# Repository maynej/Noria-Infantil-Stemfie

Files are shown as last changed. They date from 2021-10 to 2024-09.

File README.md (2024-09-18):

# Nòria Infantil Stemfie  

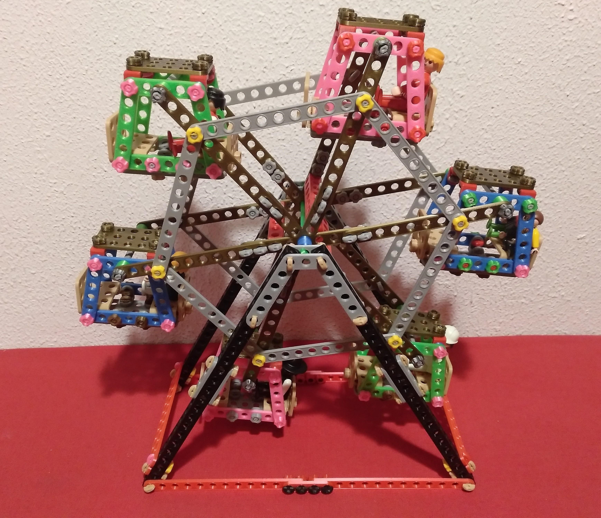
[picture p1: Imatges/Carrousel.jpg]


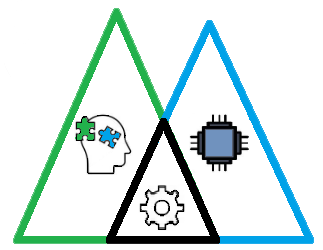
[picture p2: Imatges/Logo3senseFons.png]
Realitzada per [Jordi Mayné](https://github.com/maynej) des de Mechatronic Study 

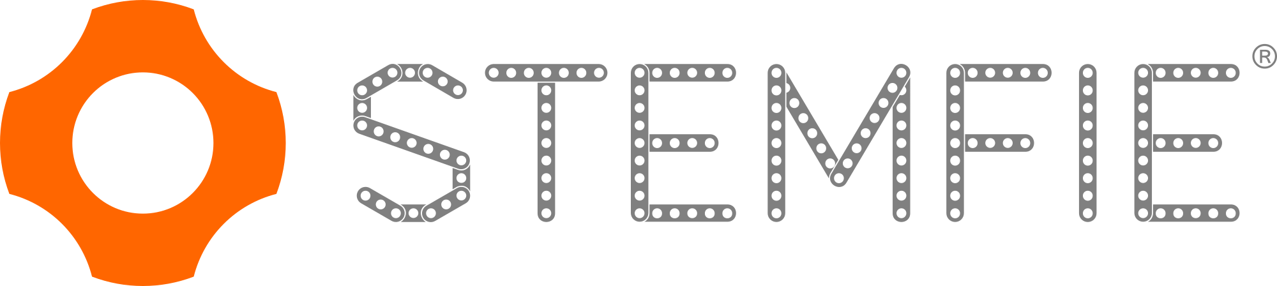
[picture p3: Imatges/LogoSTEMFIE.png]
STEMFIE es un projecte de construcció lliure, que s'imprimeix en 3D (http://stemfie.org) 

Electronics Stemfie es una llibreria STL de suports per tarjes de control, sensors i actuadors amb compatibilitat Stemfie.

[Electronics Suports amb compatibilitat Stemfie](https://github.com/maynej/Electronics-Stemfie), pretén facilitar l'automatització de les construccions amb targes Arduino, Microbit, ESP... 

La documentació està disponible també en castellà i anglés [en PDF](https://github.com/maynej/Carrousel-Stemfie/tree/main/Doc) i un video del muntatge.

STL per imprimir la Cabina [aquí](https://github.com/maynej/Carrousel-Stemfie/tree/main/STL/Cabin)

STL per imprimir la Roda [aquí](https://github.com/maynej/Carrousel-Stemfie/tree/main/STL/Wheel)

STL per imprimir la Base [aquí](https://github.com/maynej/Carrousel-Stemfie/tree/main/STL/Base)

## Cabina 

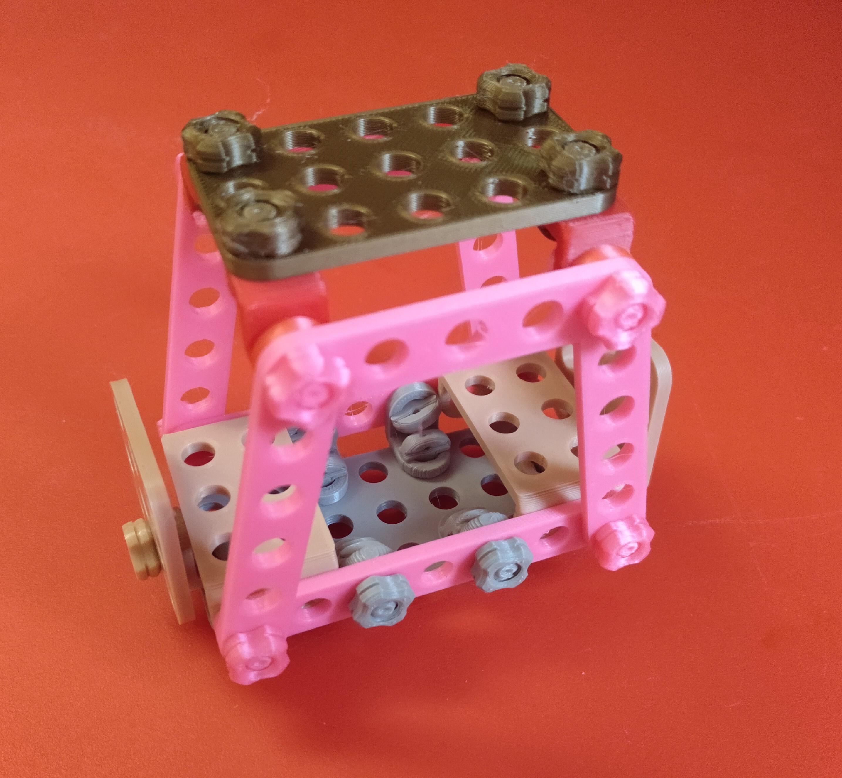
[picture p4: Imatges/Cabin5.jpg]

  
Descripció    | Quantitat     | Imatge          | Arxiu         
------------- | ------------- | --------------- | -----
Tensor 7 | 12  | | [Tensor 7](STL/Cabin/Brace_7-SPN-BRC-0006_x12.stl)
Marc Cabina | 12 | | [Marc Cabina](STL/Cabin/STR_STD_BRT_AZ_5x5x5_x12.stl)
Femella | 144 | | [Femella](STL/Cabin/NutRH-BU01.00x5mm_x144.stl)
Cargol BU00.50 | 96 | | [Cargol BU00.50](STL/Cabin/ScrewRHD-RH-BU00.50_x96.stl)
Cargol BU00.75 | 48 | | [Cargol BU00.75](STL/Cabin/Screw-RHD-RH-BU00.75_x32.stl)
Escaire | 60 | | [Escaire](STL/Cabin/STR_STD_BRD_AY-1x1_90_x60.stl)
Seient | 12 | | [Seient](STL/Cabin/STR_STD_BRT-AYx1x3x1_x12.stl)
Placa 3x3 | 12 | | [Placa 3x3](STL/Cabin/STR_STD_BRM_3x3_x12.stl)
Placa 3x5 | 6 | | [Placa 3x5](STL/Cabin/STR_STD_BRM_5x3_x6.stl)
Placa 3x7 | 6 | | [Placa 3x7](STL/Cabin/STR_STD_BRM_7x3_x6.stl)
Volandera 5mm | 24 | | [Volandera 5mm](STL/Cabin/Washer-FRE-BU01.00x00.25_x24.stl)

## Roda 

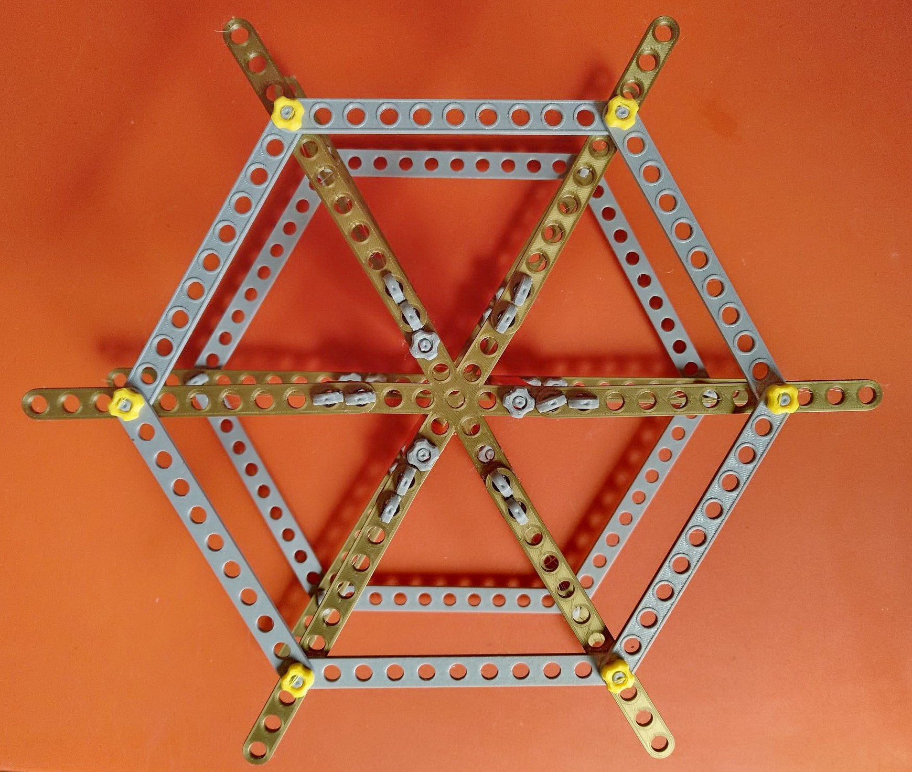
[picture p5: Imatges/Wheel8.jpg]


Descripció    | Quantitat     | Imatge          | Arxiu         
------------- | ------------- | --------------- | ----- 
Tensor 11 | 24  | | [Tensor 11](STL/Wheel/Brace_11_STR_ERR_x24.stl)
Biga 6 | 3 | | [Biga 6](STL/Wheel/beam1x1x6_3.stl)
Creu 9x9x9 | 2  | | [Creu](STL/Wheel/Cross_9x9x9_x2.stl)
Femella | 63 | | [Femella](STL/Wheel/Nut_RH_BU01.00x5mm_x39.stl)
Cargol BU00.50 | 24  | | [Cargol BU00.50](STL/Wheel/Screw_RHD_RH_BU00.50_x24.stl)
Cargol BU00.75 | 12  | | [Cargol BU00.75](STL/Wheel/Screw_RHD_RH_BU00.75_x12.stl)
Cargol BU06.50 | 3   | | [Cargol BU06.50](STL/Wheel/Screw_RHD_RH_BU06.50_x3.stl)
Pin | 6  | | [Pin BU07.00](STL/Wheel/Pin_CL_RHD_BU07.00_x6.stl)
Fixador | 6  | | [Fixador](STL/Wheel/Nut_PH_CL_BU1x5mm.stl)
Volandera 10mm | 12  | | [Volandera 12 mm](STL/Wheel/Washer10mm_12.stl)

## Base 

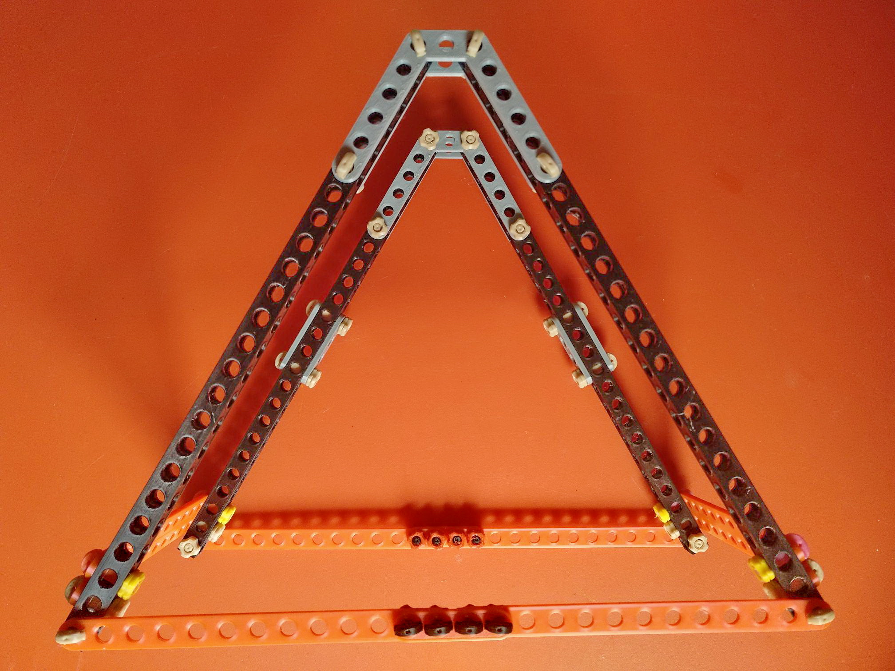
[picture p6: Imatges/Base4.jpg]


Descripció    | Quantitat     | Imatge          | Arxiu         
------------- | ------------- | --------------- | ----- 
Biga 12 | 8 | | [Biga 12](STL/Base/Beam_12_x8.stl)
Tensor 4 | 10  | | [Tensor 4](STL/Base/Brace_4_STR_ERR_BU04x01x00.25_x10.stl)
Tensor 12 | 4  | | [Tensor 12](STL/Base/Brace_12_STR_ERR_BU12x01x00.25x4.stl)
Tensor 13 | 4  | | [Tensor 13](STL/Base/Brace_13_STR_ERR_BU13x01x00.25_x4.stl)
Femella | 44 | | [Femella](STL/Base/Nut_RH_BU01.00x5mm_x44.stl)
Cargol BU00.50 | 8  | | [Cargol BU00.50](STL/Base/Screw_RHD_RH_BU00.50_x8.stl)
Cargol BU01.25 | 12 | | [Cargol BU01.25](STL/Base/Screw_RHD_RH_BU01.25_x12.stl)
Cargol BU01.50 | 16 | | [Cargol BU01.50](STL/Base/Screw_RHD_RH_BU01.50_x16.stl)
Pin | 1  | | [Pin Eix](STL/Base/Pin166.stl)
Fixador | 1  | | [Fixador](STL/Base/Nut_PH_CL_BU1x5mm_x1.stl)
U | 4 | | [U](STL/Base/STR_STD_BRT_AZ_3_5_5_120_x4.stl)
Volandera | 13  | | [Volandera](STL/Base/Washer_FRE_BU01.00x00.25_x13.stl)

## Control 

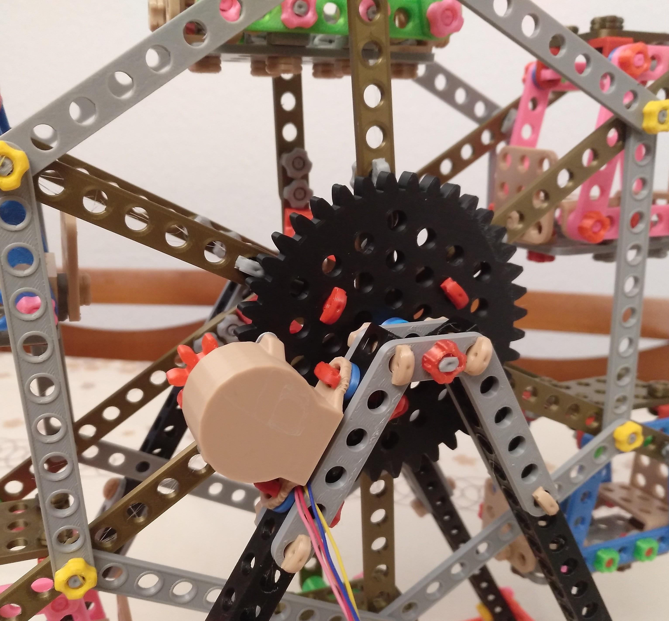
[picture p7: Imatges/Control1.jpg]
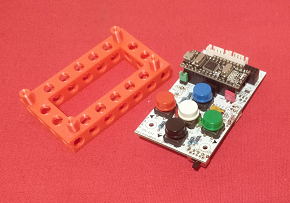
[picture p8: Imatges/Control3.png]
 

Descripció    | Quantitat     | Imatge          | Arxiu         
------------- | ------------- | --------------- | ----- 
Femella | 5 | | [Femella](STL/Control/Nut_RH_BU01.00x5mm_x2.stl)
Cargol BU01.50 | 5 | | [Cargol BU01.50](STL/Control/Screw_RHD_RH_BU01.50_x5.stl)
CPU suport | 1 | | [CPU Suport](STL/Control/CPUEscornaStemfie_x1.stl)
Volandera 2.5mm | 2  | | [Volandera](STL/Control/Washer_FRE_2.5mmx2.stl)
Engranatge motor | 1  | | [Engranatge motor](STL/Control/Gear_28BYJ-48_x1.stl)
Engranatge 40 |  1  | | [Engranatge 40](STL/Control/IGE_0.5_40_M2,5_x1.stl)
Suport motor |  1  | | [Suport motor](STL/Control/28BYJ-48_4H_x1.stl)

## Mesurador Stemfie 

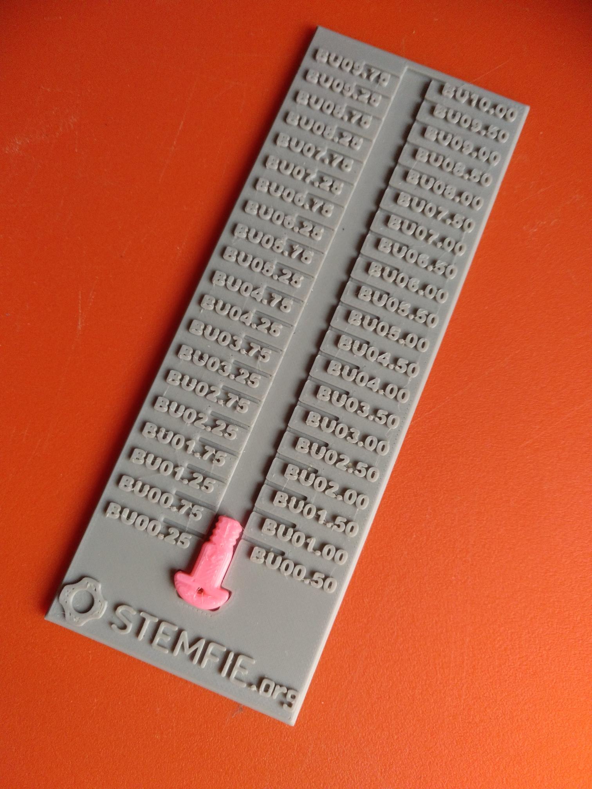
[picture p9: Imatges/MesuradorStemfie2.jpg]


Descripció    | Opcional     | Arxiu         
------------- | ------------ | ----- 
Mesurador Cargols | 1  | [Mesurador](STL/Base/MesuraStemfie2.stl)

## QR


## Llicència

Creative Commons Attribution-NoComercial-ShareAlike 4.0 International (CC BY-NC-SA 4.0)

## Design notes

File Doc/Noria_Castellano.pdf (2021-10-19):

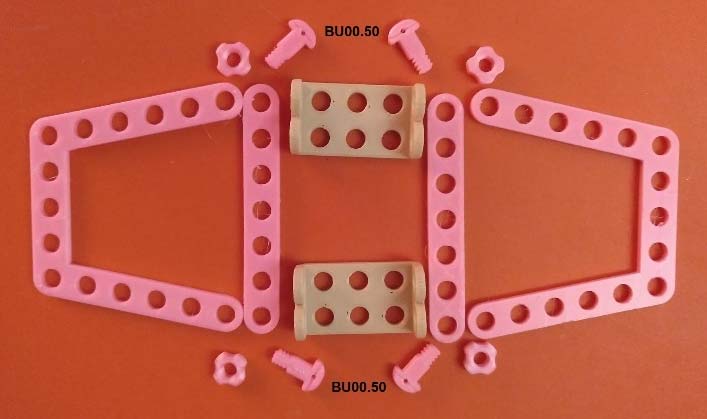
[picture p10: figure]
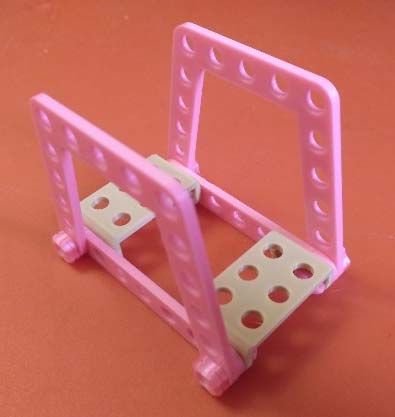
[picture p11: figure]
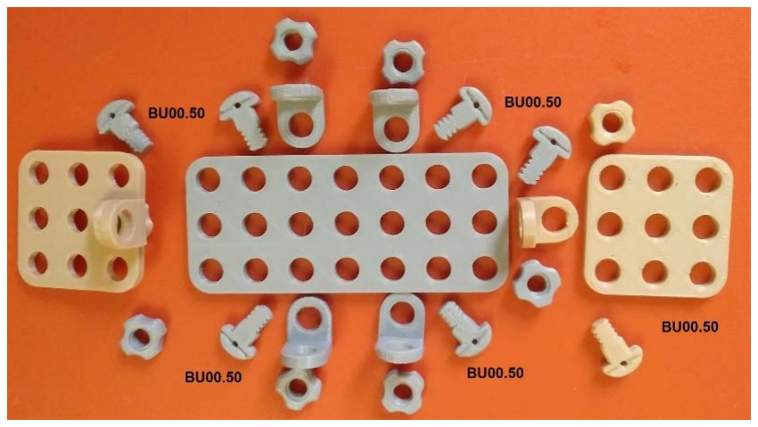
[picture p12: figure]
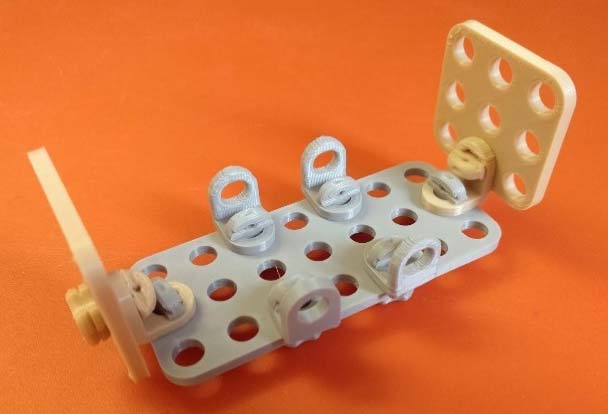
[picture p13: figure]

NORIA INFANTIL V1 – 2021 | 1 | JORDI MAYNE

## Noria Infantil

Esta Noria es una reproducción de la típica atracción infantil hecha con estructura Stemfie.

Permite ser una herramienta de habilidad de montaje para grupos, la conforman 6 cabinas idénticas, las 2 ruedas de soporte de las cabinas y la estructura de la base, es decir que pueden participar hasta 9 jóvenes o adolescentes.

Los tornillos son piezas que actualmente no se usan en los montajes actuales, se unen las piezas a base de ensamblajes fáciles, pero a la vez pierden la oportunidad de coger una habilidad manual y destreza para colocar los mismos y girar la tuercas.

### Montaje

Cabina

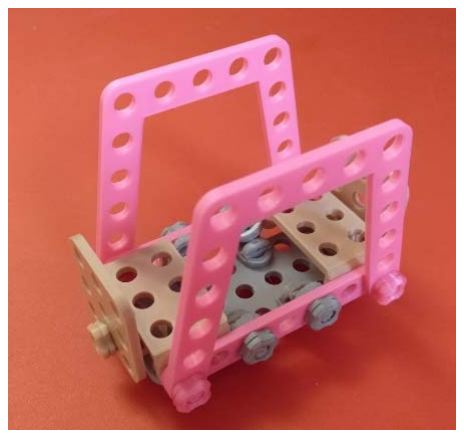
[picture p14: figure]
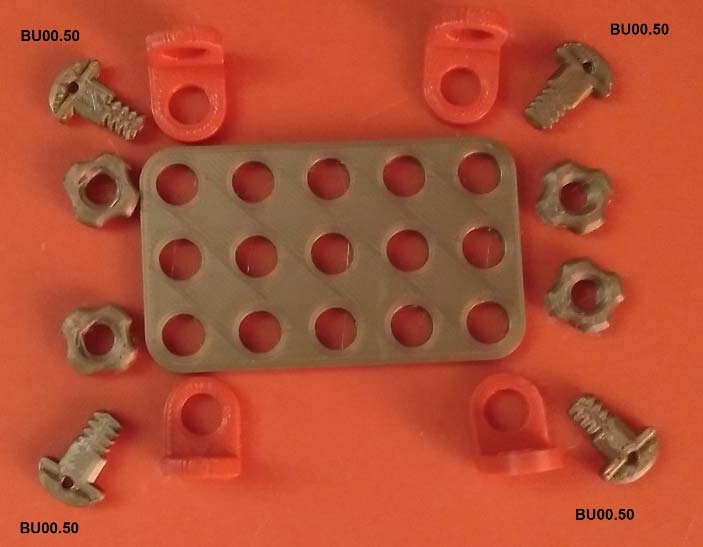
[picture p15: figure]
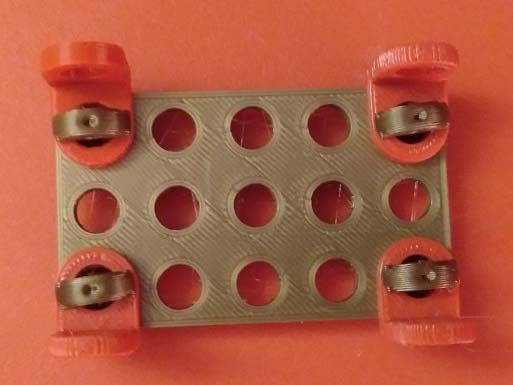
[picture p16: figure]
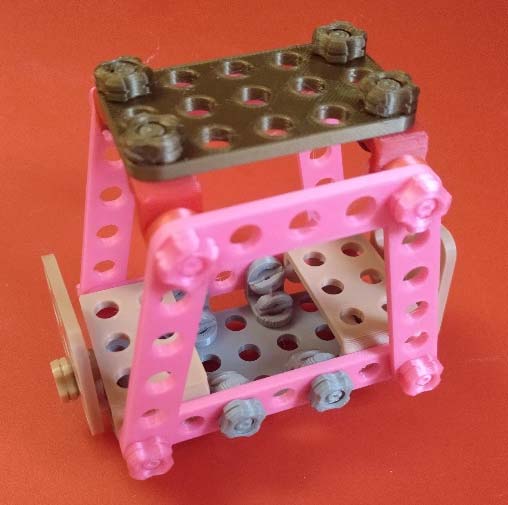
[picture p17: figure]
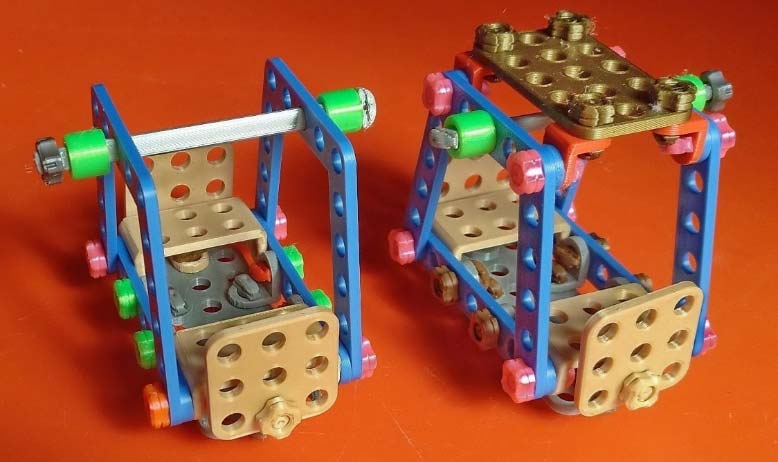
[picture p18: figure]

NORIA INFANTIL V1 – 2021 | 2 | JORDI MAYNE

Si se quiere la versión con techo, para el invierno hace falta añadir este montaje. Los tornillos son del tipo BU00.50

Todos los tormillos son del tipo BU00.50

La cabina puede quedar en este punto, versión sin techo, para el verano.

Para fijar el techo a la cabina hace falta añadir 4 tornillos BU00.75, 4 arabdelas y 4 tuercas.

Se montan 6 cabinas y para fijarlas a la rueda se usa PIN07.00, fijador, y arandelas de 10mm, se verá más adelante este montaje.

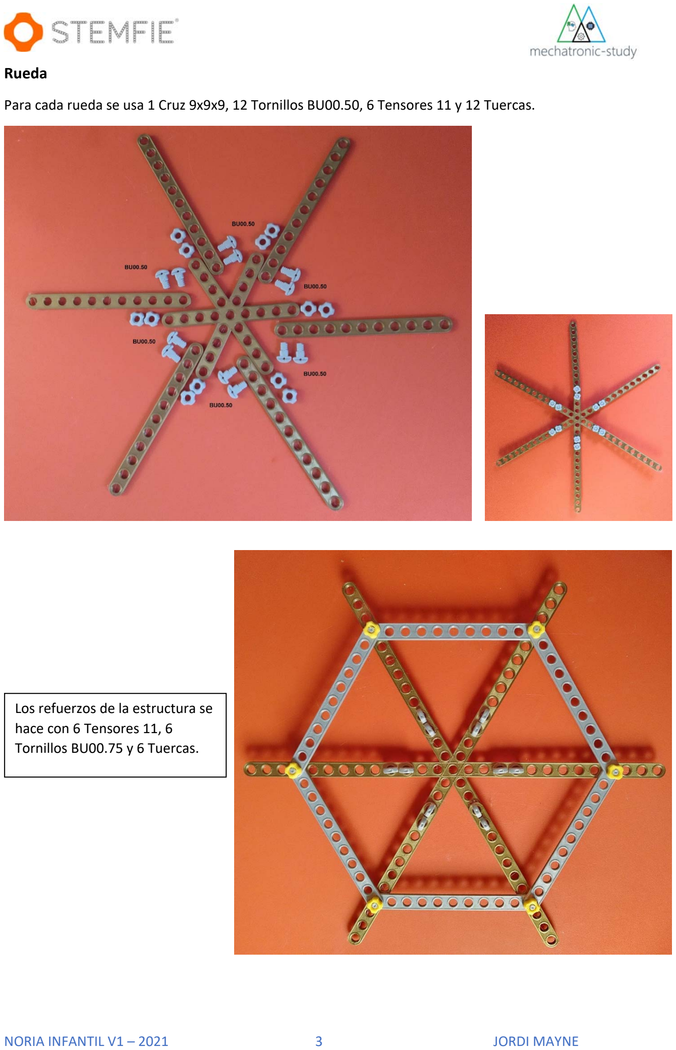
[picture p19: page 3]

NORIA INFANTIL V1 – 2021 | 3 | JORDI MAYNE

Rueda

Para cada rueda se usa 1 Cruz 9x9x9, 12 Tornillos BU00.50, 6 Tensores 11 y 12 Tuercas.

Los refuerzos de la estructura se hace con 6 Tensores 11, 6
Tornillos BU00.75 y 6 Tuercas.

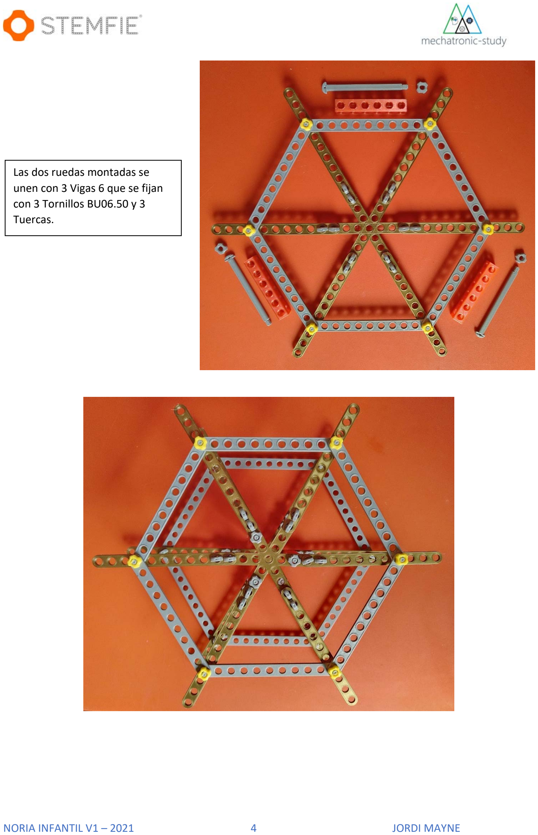
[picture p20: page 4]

NORIA INFANTIL V1 – 2021 | 4 | JORDI MAYNE

Las dos ruedas montadas se unen con 3 Vigas 6 que se fijan con 3 Tornillos BU06.50 y 3 Tuercas.

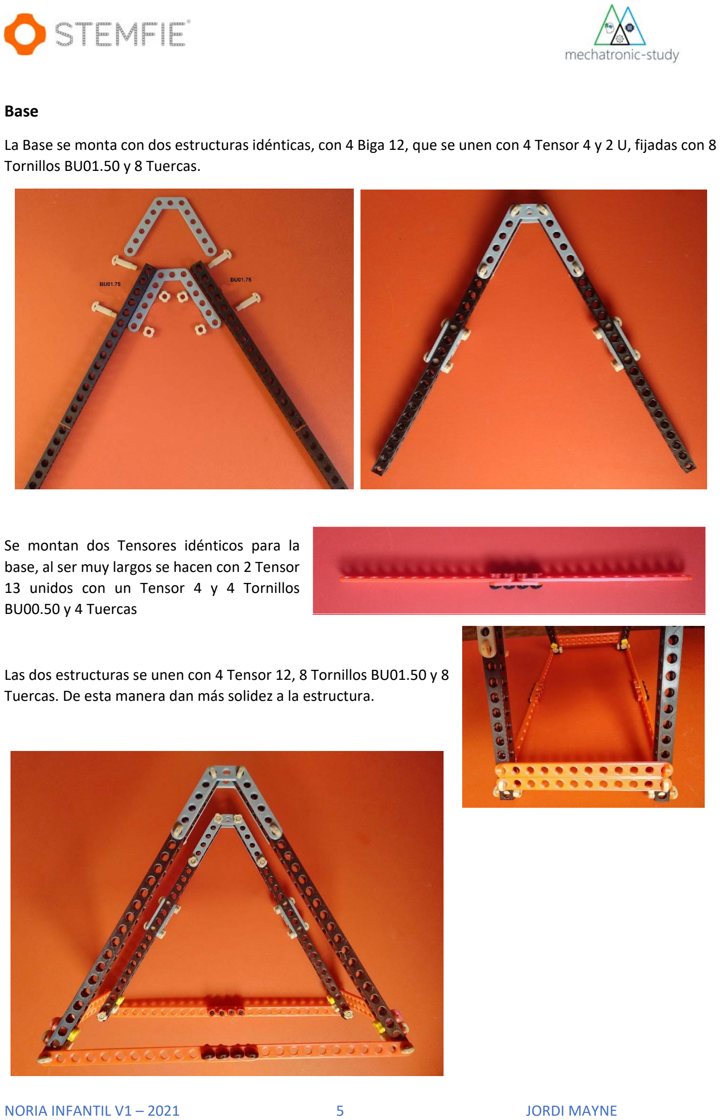
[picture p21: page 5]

NORIA INFANTIL V1 – 2021 | 5 | JORDI MAYNE

Base

La Base se monta con dos estructuras idénticas, con 4 Biga 12, que se unen con 4 Tensor 4 y 2 U, fijadas con 8 Tornillos BU01.50 y 8 Tuercas.

Se montan dos Tensores idénticos para la base, al ser muy largos se hacen con 2 Tensor 13 unidos con un Tensor 4 y 4 Tornillos BU00.50 y 4 Tuercas

Las dos estructuras se unen con 4 Tensor 12, 8 Tornillos BU01.50 y 8 Tuercas. De esta manera dan más solidez a la estructura.

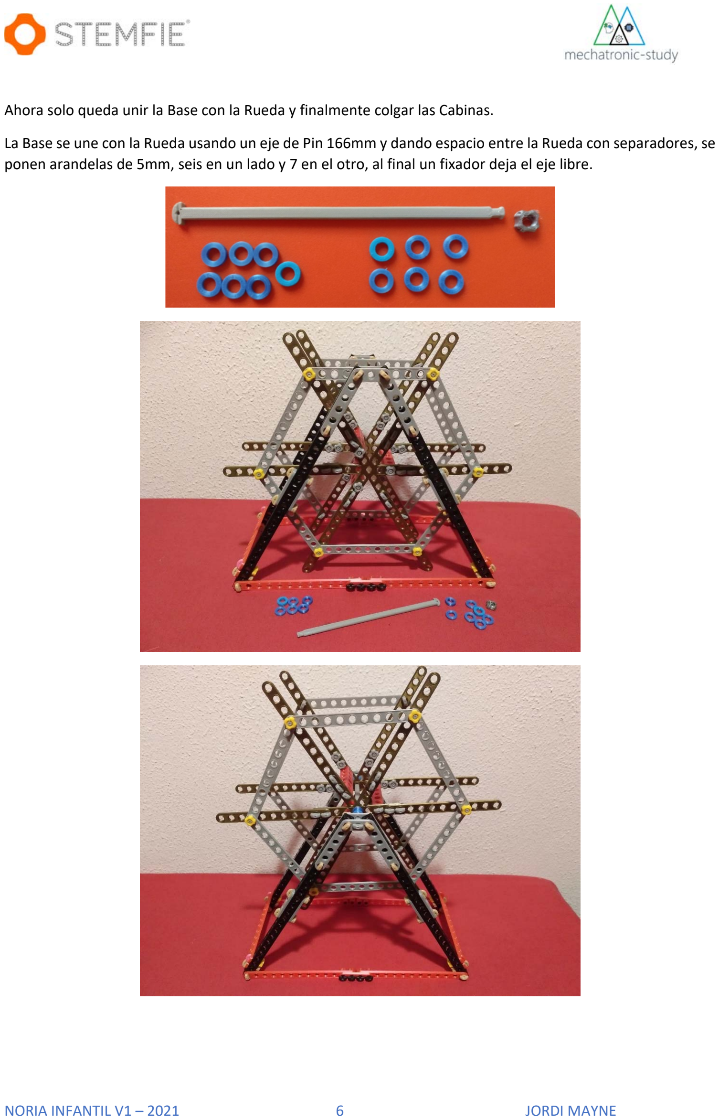
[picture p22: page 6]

NORIA INFANTIL V1 – 2021 | 6 | JORDI MAYNE

Ahora solo queda unir la Base con la Rueda y finalmente colgar las Cabinas.

La Base se une con la Rueda usando un eje de Pin 166mm y dando espacio entre la Rueda con separadores, se ponen arandelas de 5mm, seis en un lado y 7 en el otro, al final un fixador deja el eje libre.

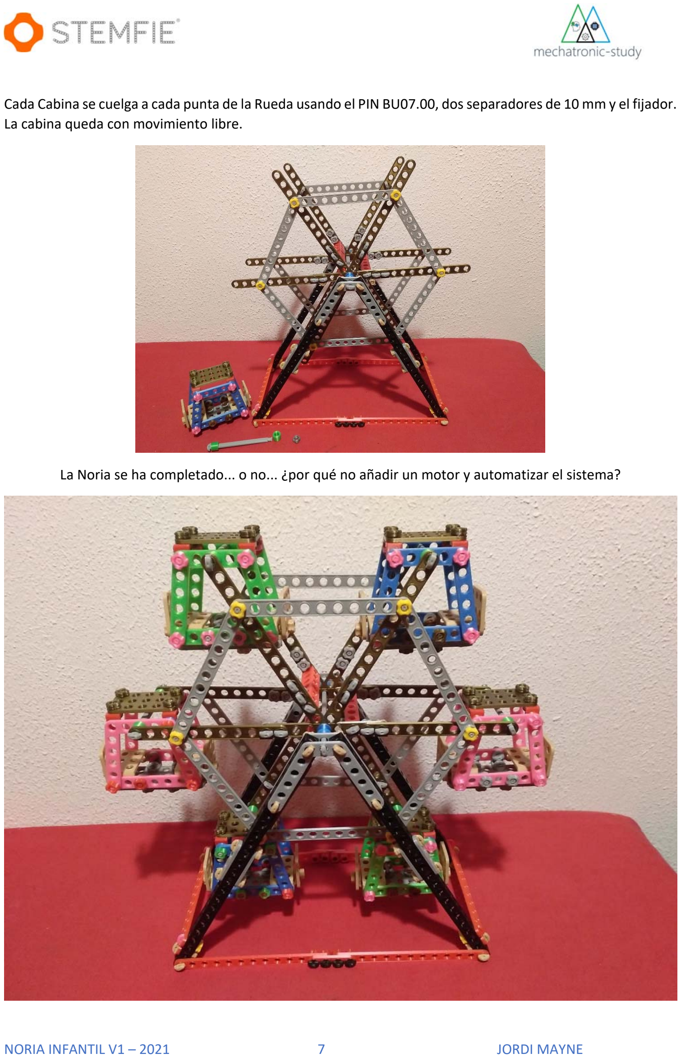
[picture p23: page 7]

NORIA INFANTIL V1 – 2021 | 7 | JORDI MAYNE

Cada Cabina se cuelga a cada punta de la Rueda usando el PIN BU07.00, dos separadores de 10 mm y el fijador. La cabina queda con movimiento libre.

La Noria se ha completado... o no... ¿por qué no añadir un motor y automatizar el sistema?

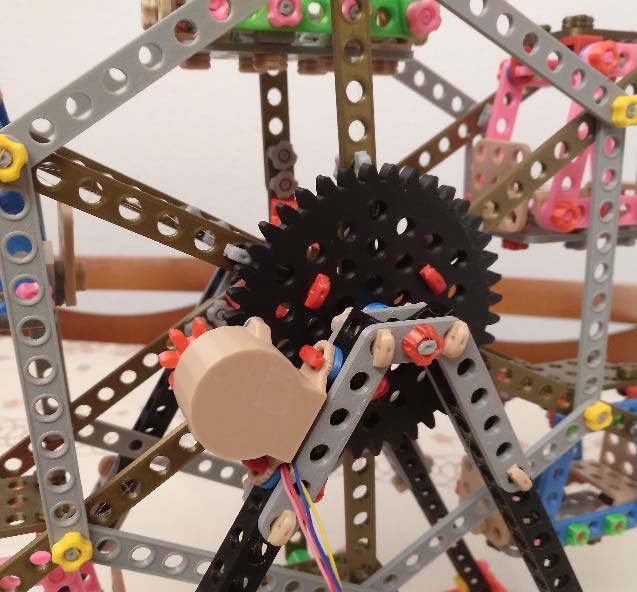
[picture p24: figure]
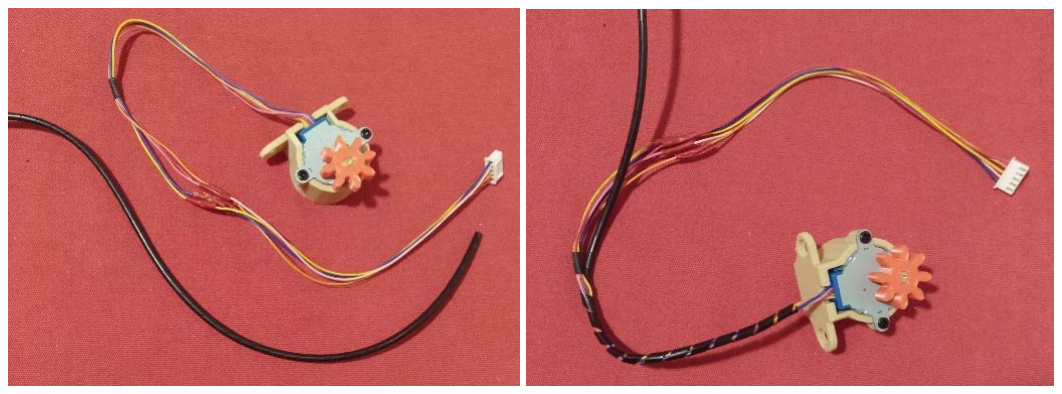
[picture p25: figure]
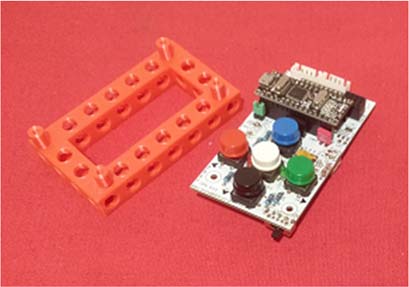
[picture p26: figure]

NORIA INFANTIL V1 – 2021 | 8 | JORDI MAYNE

Control

Para controlar/automatizar la Nòria hace falta añadir un motor para girar la rueda de la Noria, una electrónica y alimentación.

Motor: La mejor opción para el acoplamiento mecánico y el tipo de funcionamiento
es un motor paso a paso con reductora del tipo 28BYJ‐48 muy económico, con su
correspondiente engranaje que permite un movimiento preciso.

Al colocar el motor a la estructura, con su soporte correspondiente de la librería de Electronics Stemfie: https://github.com/maynej/Electronics‐Stemfie, queda ajustado con el engranaje que se fija en la Rueda de la Noria.

Con esta relación de reducción también se consigue un movimiento adecuado.

El cable del motor paso a paso no es suficientemente largo para llegar a la mesa dónde se ponga la noria, entonces hay que añadir una prolongación, tal como se ve en la siguiente imagen, después se puede añadir un tubo en espiral típico para cables.

Electrónica:

Se puede usar cualquier placa controladora tipo Arduino, Microbit, u otras, pero, una opción buena es la placa que utiliza Escornabot Singularis, con su soporte correspondiente Stemfie.

Esta placa incorpora una Arduino Nano, 5 pulsadores y un driver para el motor 28BYJ‐48, así da una solución fácil. Además, se puede usar el mismo firmware adaptándolo a las funcionalidades que se quieran.

NORIA INFANTIL V1 – 2021 | 9 | JORDI MAYNE

En la carpeta CPU de Github https://github.com/maynej/Noria‐Infantil/tree/main/CPU hay el firmware adaptado para las siguientes funciones:

Programación

Versión 1.0:

- Una pulsación al botón azul se programa una vuelta entera. Si se hacen dos pulsaciones programa dos vueltas y así sucesivamente.
- Una pulsación al botón negro se programa una vuelta entera en sentido contrario. Si se dan dos pulsaciones programa da dos vueltas i así sucesivamente.
- Una pulsación al botón blanco ejecuta/para los movimientos programados. Si cuando está en marcha se hace una pulsación del botón blanco se para el motor.
- Una pulsación al botón rojo se programa el avance de una cabina hasta la cabina siguiente. Si se dan dos pulsaciones programa el desplazamiento de dos cabinas y así sucesivamente.
- Una pulsación al botón verde se programa el avance de una cabina hasta la siguiente, en sentido contrario. Si se dan dos pulsaciones programa el desplazamiento de dos cabinas i así sucesivamente.

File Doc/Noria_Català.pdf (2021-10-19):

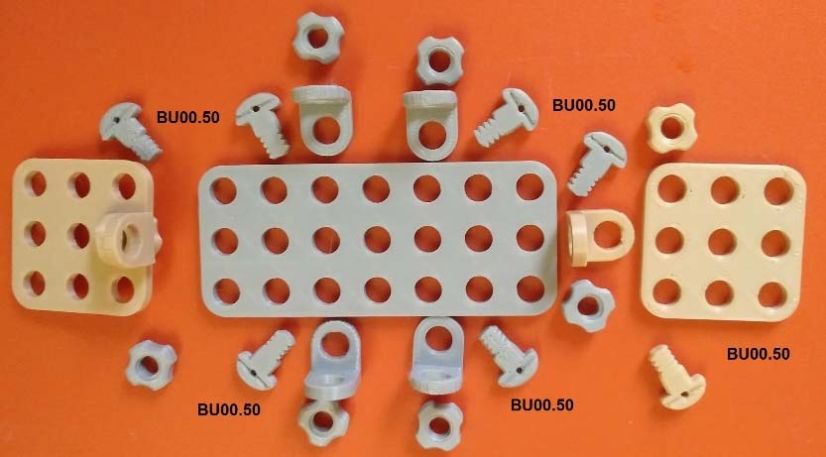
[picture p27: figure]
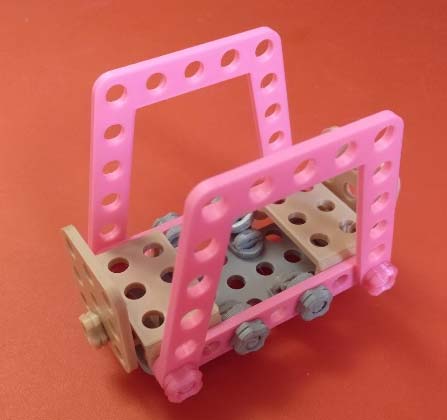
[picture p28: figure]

NÒRIA INFANTIL V1 – 2021 | 1 | JORDI MAYNE

## Nòria Infantil

Aquesta nòria es una reproducció de la típica atracció infantil feta amb estructura Stemfie.

Permet ser una eina d’habilitat de muntatge per grups, la formen 6 cabines idèntiques, les 2 rodes de suport de les cabines i l’estructura de la base, es a dir que poden participar fins a 9 infants o adolescents.

Els cargols son peces que actualment no es fan servir en els muntatges comercials, s’uneixen les peces a base d’assemblatges fàcils, però, a la vegada perden l’oportunitat d’agafar una habilitat manual i destresa per col∙locar els mateixos.

### Muntatge

Cabina

Tots els cargols son del tipus BU00.50

La cabina pot quedar en aquest punt, versió sense sostre per l’estiu.

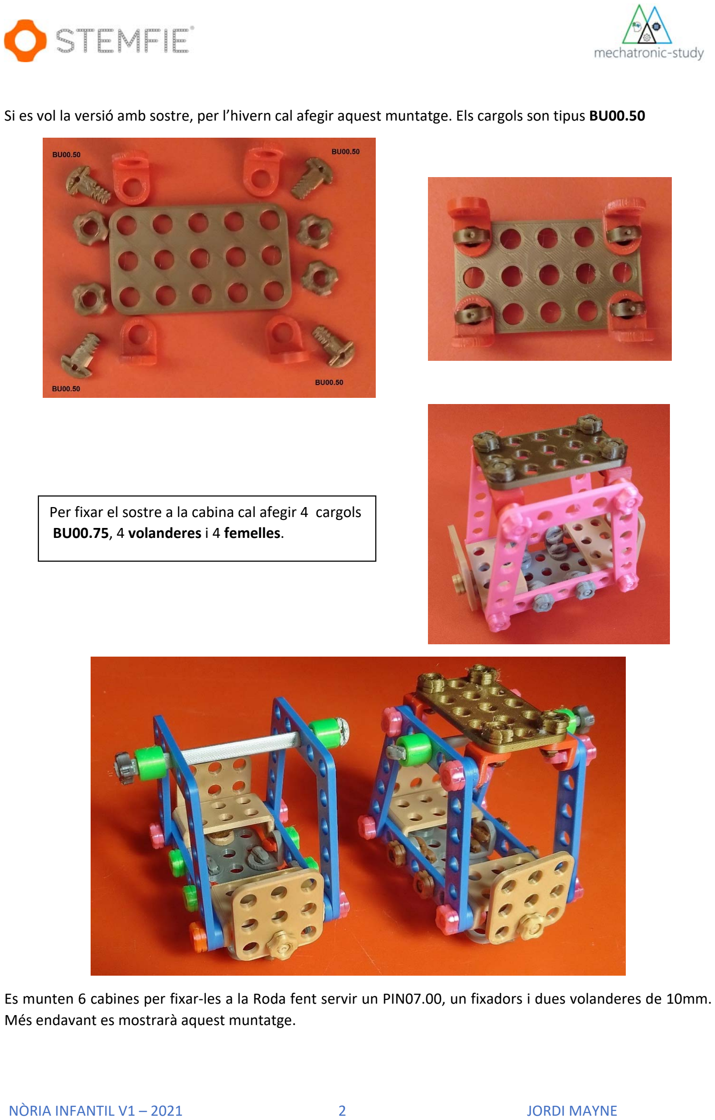
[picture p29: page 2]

NÒRIA INFANTIL V1 – 2021 | 2 | JORDI MAYNE

Si es vol la versió amb sostre, per l’hivern cal afegir aquest muntatge. Els cargols son tipus BU00.50

Es munten 6 cabines per fixar‐les a la Roda fent servir un PIN07.00, un fixadors i dues volanderes de 10mm. Més endavant es mostrarà aquest muntatge.

Per fixar el sostre a la cabina cal afegir 4 cargols BU00.75, 4 volanderes i 4 femelles.

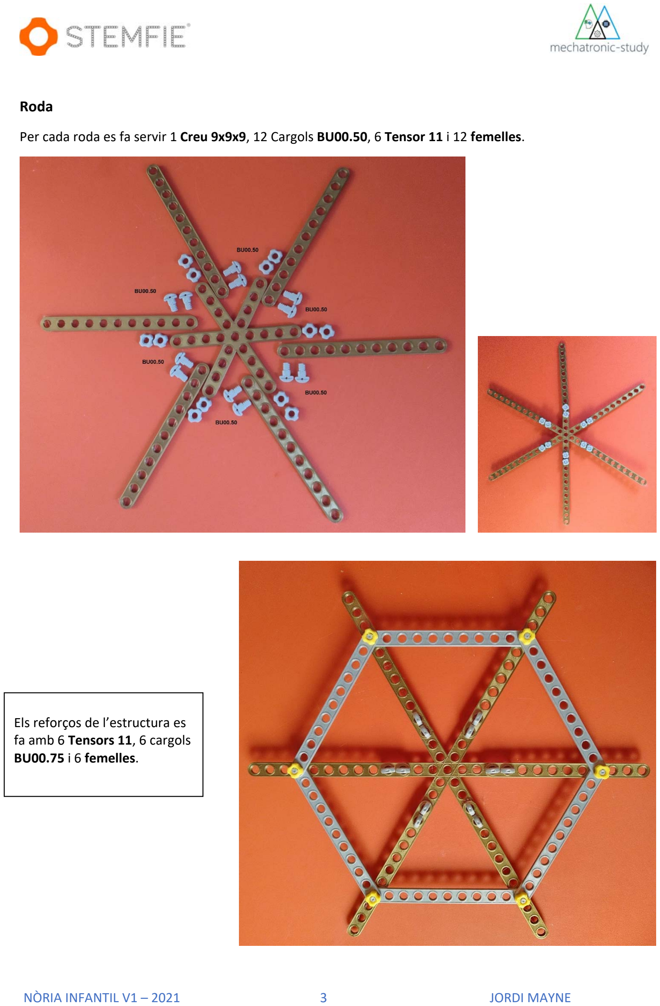
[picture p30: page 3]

NÒRIA INFANTIL V1 – 2021 | 3 | JORDI MAYNE

Roda

Per cada roda es fa servir 1 Creu 9x9x9, 12 Cargols BU00.50, 6 Tensor 11 i 12 femelles.

Els reforços de l’estructura es fa amb 6 Tensors 11, 6 cargols BU00.75 i 6 femelles.

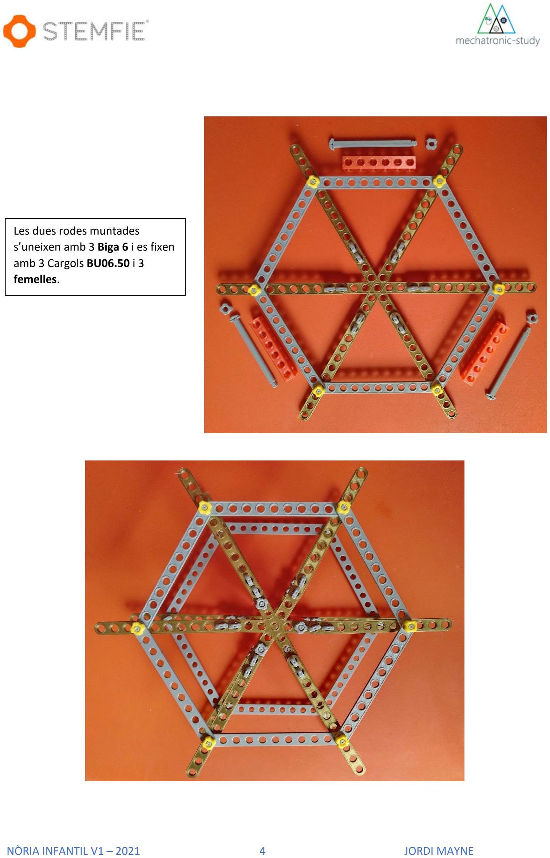
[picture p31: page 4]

NÒRIA INFANTIL V1 – 2021 | 4 | JORDI MAYNE

Les dues rodes muntades
s’uneixen amb 3 Biga 6 i es fixen amb 3 Cargols BU06.50 i 3
femelles.

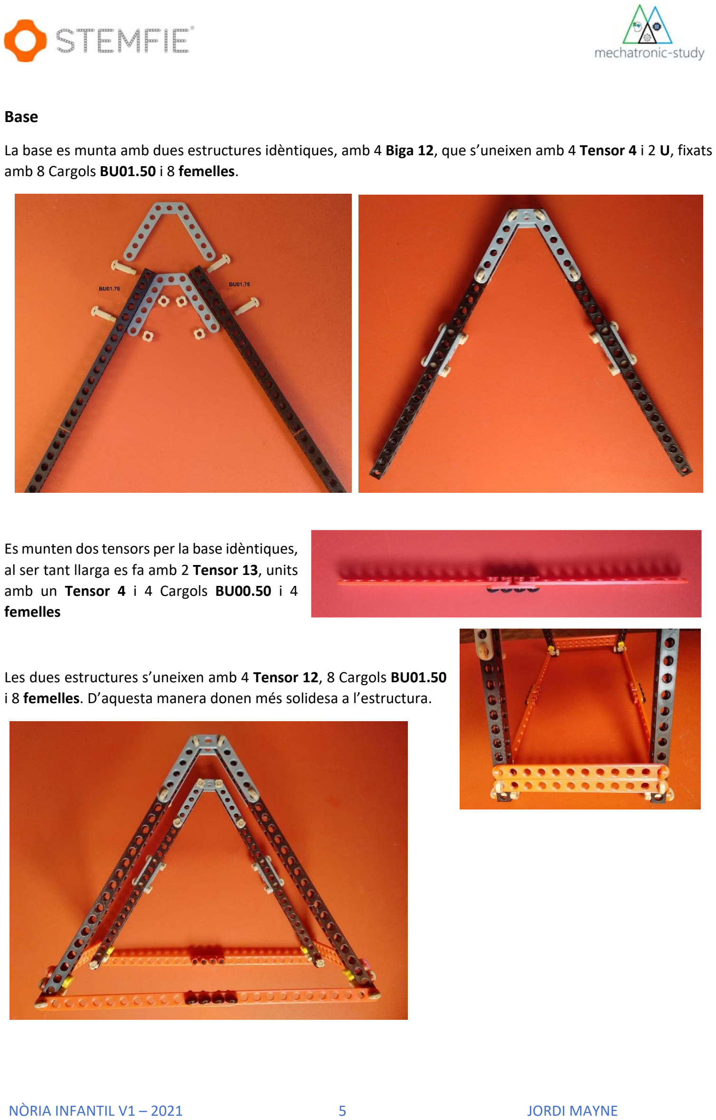
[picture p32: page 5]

NÒRIA INFANTIL V1 – 2021 | 5 | JORDI MAYNE

Base

La base es munta amb dues estructures idèntiques, amb 4 Biga 12, que s’uneixen amb 4 Tensor 4 i 2 U, fixats amb 8 Cargols BU01.50 i 8 femelles.

Es munten dos tensors per la base idèntiques, al ser tant llarga es fa amb 2 Tensor 13, units amb un Tensor 4 i 4 Cargols BU00.50 i 4 femelles

Les dues estructures s’uneixen amb 4 Tensor 12, 8 Cargols BU01.50 i 8 femelles. D’aquesta manera donen més solidesa a l’estructura.

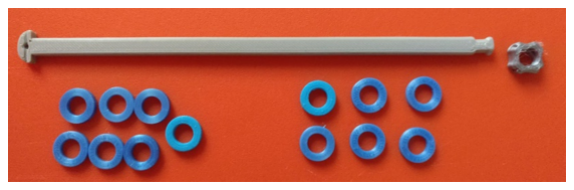
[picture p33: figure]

NÒRIA INFANTIL V1 – 2021 | 6 | JORDI MAYNE

Ara només queda unir la Base amb la Roda i finalment penjar les Cabines.

La Base s’uneix amb la Roda fent servir un eix de Pin 166mm i donar espai entre la Roda i com a separadors es posen volanderes de 5mm, 5 en una banda i 2 a l’altre, al final un fixador amb una volandera deixa l’eix ferm.

Cada Cabina es penja a cada punta de la Roda fent servir el PIN BU07.00 dues volanderes de 10 mm i el fixador. La cabina queda amb moviment lliure.


NÒRIA INFANTIL V1 – 2021 | 7 | JORDI MAYNE

La Nòria està completada... o no... perquè no afegir un motor i automatitzar el sistema?


NÒRIA INFANTIL V1 – 2021 | 8 | JORDI MAYNE

Control

Per controlar/automatitzar la Nòria cal afegir un motor per girar la roda de la Nòria, una electrònica i alimentació.

Motor: La millor opció per acoblament mecànic i tipus de funcionament es un motor
pas a pas amb reductora del tipus 28BYJ‐48, molt econòmic, amb el seu corresponent
engranatge que permet un moviment preciso.

Al col∙locar el motor a l’estructura, amb el seu suport corresponent de la llibreria de Electronics Stemfie: https://github.com/maynej/Electronics‐Stemfie, queda ajustat amb l’engranatge que es fixa en la Roda de la Nòria.

Amb aquesta relació de reducció també s’aconsegueix un moviment adequat.

El cable del motor pas a pas no es prou llarg per arribar a la taula on es posi la nòria, llavors cal afegir una prolongació, tal com es veu en la següent imatge, desprès es pot afegir un tub en espiral típic per cables.

Electrònica:

Es pot fer servir qualsevol placa controladora tipus Arduino, Microbit, o d’altres, però, una opció força escaient es la placa que utilitza Escornabot Singularis, amb el seu suport corresponent Stemfie.

Aquesta placa incorpora una Arduino Nano, 5 polsadors i el driver per el motor 28BYJ‐48, així dona una solució fàcil. A més es pot fer servir el mateix firmware adaptant‐lo a les funcionalitats que vulguem.

NÒRIA INFANTIL V1 – 2021 | 9 | JORDI MAYNE

En la carpeta CPU de Github https://github.com/maynej/Noria‐Infantil/tree/main/CPU hi ha el firmware adaptat per les següents funcions:

Programació

Versió 1.0:

- Una pulsació al botó blau es programa una volta sencera. Si es fan dues pulsacions programa dues voltes i així successivament.
- Una pulsació al botó negre es programa una volta sencera en sentit contrari. Si es fan dues pulsacions programa dona dues voltes i així successivament.
- Una pulsació al botó blanc executa/para els moviments programats. Si quan està en marxa es fa una pulsació del botó blanc es para el motor.
- Un pulsació al botó vermell es programa el moviment d’una cabina fins la cabina següent. Si es fan dues pulsacions programa el desplaçament de dues cabines i així successivament.
- Un pulsació al botó verd es programa el moviment d’una cabina fins la següent, en sentit contrari. Si es fan dues pulsacions programa el desplaçament de dues cabines i així successivament.

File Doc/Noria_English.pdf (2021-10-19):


NÒRIA INFANTIL V1 – 2021 | 1 | JORDI MAYNE

## Children's Ferris Wheel

This Ferris Wheel is a reproduction of the typical children's attraction made with Stemfie parts.

This project is suitable for assembly ability for groups; it contains six identical cabins, two support wheels, and a base. It is helpful to be able to participate in up to nine children or teenagers.

Screws are parts that are not currently used in current assemblies, the pieces are joined together based on simple assemblies, but at the same time, they lose the opportunity to take a manual skill and dexterity to place them.

### Assembly

Cabin

All screws are type BU00.50

The cabin can be left at this point, a roofless version for the summer.


NÒRIA INFANTIL V1 – 2021 | 2 | JORDI MAYNE

If you want the roofed version, you need to add this attachment for the winter. The screws are type BU00.50.

Six cabins are mounted, and to fix them to the wheel using PIN07.00, fastener, and 10mm washers, this assembly will be shown later.

To fix the roof to the cabin, you need to add four screws BU00.75, four washers and four nuts.


NÒRIA INFANTIL V1 – 2021 | 3 | JORDI MAYNE

Wheel

For each wheel, use the following parts: Cross 9x9x9 (1 piece), Screw BU00.50 (12 pieces), 6 Braces BU11 and Nuts (12 pieces).

Reinforcements of the structure is made with six braces BU11, six screws BU00.75 and six Nuts.


NÒRIA INFANTIL V1 – 2021 | 4 | JORDI MAYNE

The two mounted wheels are joined with three Beam 6 and fixed with three screw BU06.50 and three Nuts.


NÒRIA INFANTIL V1 – 2021 | 5 | JORDI MAYNE

Base

The base is mounted with two identical structures containing four Beam BU12, joined by four braces BU4 and two U, fixed with eight screws BU01.50 and eight Nuts.

Two identical braces are mounted for the base, being so long it is done with two brace BU13 joined with a brace BU4 and four screw BU00.50 and four Nuts.

The two structures are joined by four brace BU12, eight screws BU01.50 and 8 Nuts. In this way, they give more solidity to the structure.


NÒRIA INFANTIL V1 – 2021 | 6 | JORDI MAYNE

Now all that remains is to join the Base with the Wheel and finally hang the Cabins.

The Base joins the Wheel using a PIN 166mm shaft and give space between the wheel putting 5mm washers as separators, six on one side and seven on the other side, at the end a fastener leaves the shaft free.


NÒRIA INFANTIL V1 – 2021 | 7 | JORDI MAYNE

Each Cabin is hung at each end of the Wheel using PIN BU07.00 two 10 mm washer and the fastener. The cabin moves freely.

The Ferris Wheel is complete ... or not ... why not add an engine and automate the system?


NÒRIA INFANTIL V1 – 2021 | 8 | JORDI MAYNE

Control

Para controlar/automatizar la Nòria hace falta añadir un motor para girar la rueda de la Noria, una electrónica y alimentación.

Motor: La mejor opción para el acoplamiento mecánico y el tipo de funcionamiento
es un motor paso a paso con reductora del tipo 28BYJ‐48 muy económico, con su
correspondiente engranaje que permite un movimiento preciso.

Al colocar el motor a la estructura, con su soporte correspondiente de la librería de Electronics Stemfie: https://github.com/maynej/Electronics‐Stemfie, queda ajustado con el engranaje que se fija en la Rueda de la Noria.

Con esta relación de reducción también se consigue un movimiento adecuado.

El cable del motor paso a paso no es suficientemente largo para llegar a la mesa dónde se ponga la noria, entonces hay que añadir una prolongación, tal como se ve en la siguiente imagen, después se puede añadir un tubo en espiral típico para cables.

Electrónica:

Se puede usar cualquier placa controladora tipo Arduino, Microbit, u otras, pero, una opción buena es la placa que utiliza Escornabot Singularis, con su soporte correspondiente Stemfie.

Esta placa incorpora una Arduino Nano, 5 pulsadores y un driver para el motor 28BYJ‐48, así da una solución fácil. Además se puede usar el mismo firmware adaptándolo a las funcionalidades que se quieran.


NÒRIA INFANTIL V1 – 2021 | 9 | JORDI MAYNE

Power Supply

The power supply can be from a 6Vdc transformer, a pack of four battery AA, or a 9Vdc rechargeable battery. In this case I used a 9V rechargeable battery.

In the folder CPU of Github https://github.com/maynej/Noria‐Infantil/tree/main/CPU there are the firmware adapted for the next functions:

Firmware

Version 1.0:

- Pressing one time the blue button, programs a full lap. If press two times, program two laps and so on.
- Pressing the black button, programs a full lap in the opposite direction. If press two times, program two laps and so on.
- Pressing the white button, execute/stop the programmed movements. If press white button when it is running, the engine stops.
- Pressing the red button, programs the advance one cabin to the next cabin. If press two times, it programs two cabins and so on.
- Pressing the green button, programs the advance one cabin to the next cabin, in the opposite direction. If press two times, it programs two cabins and so on.

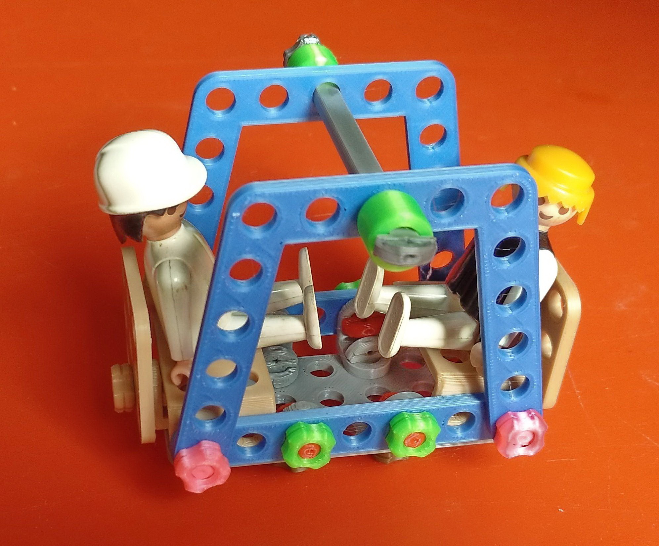
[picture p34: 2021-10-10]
Imatges/CabinaLego.jpg

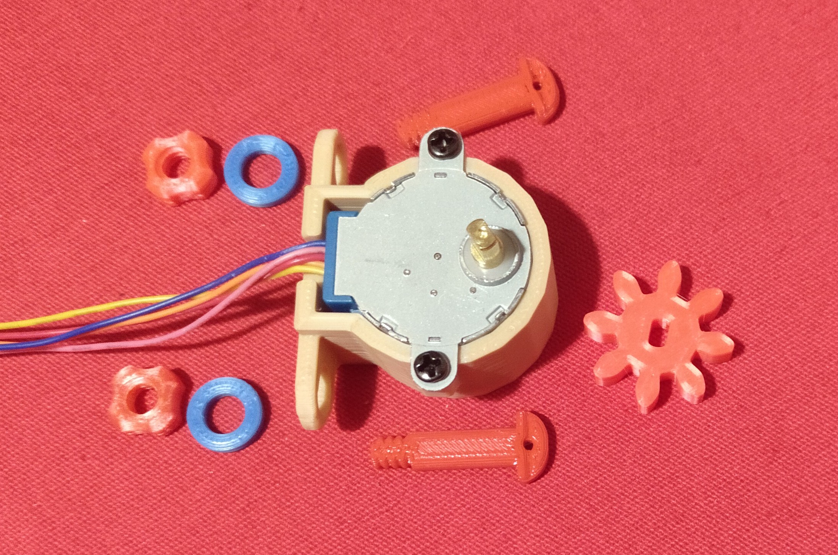
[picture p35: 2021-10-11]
Imatges/Control2.jpg

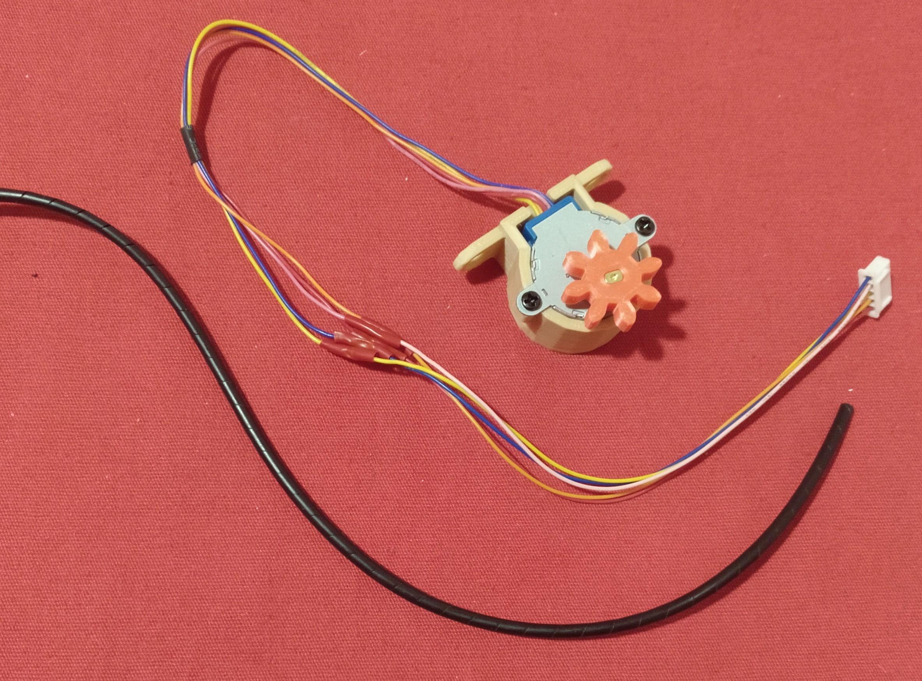
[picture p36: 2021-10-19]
Imatges/Control5.jpg

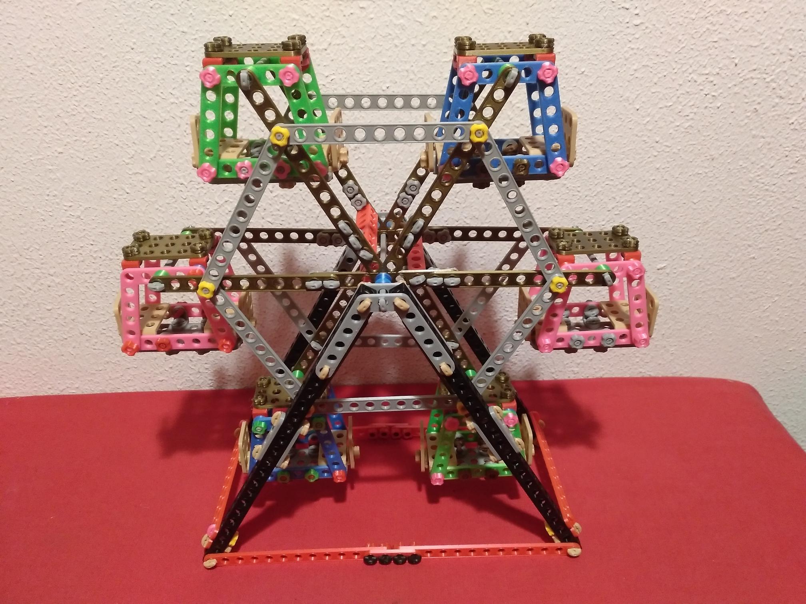
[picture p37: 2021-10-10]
Imatges/Muntatge4.jpg

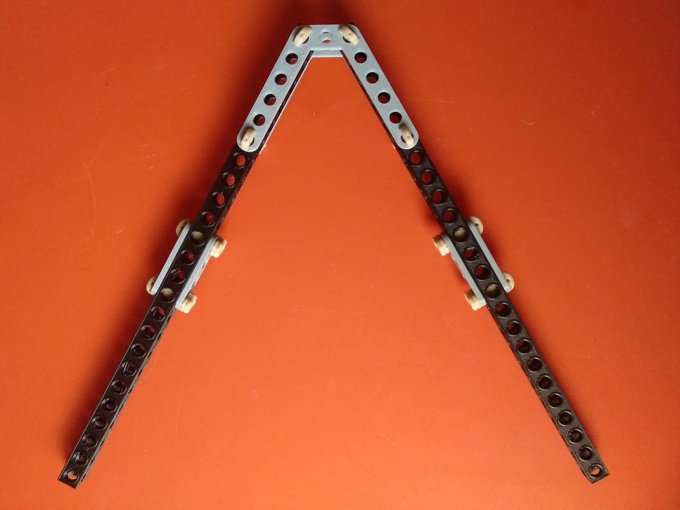
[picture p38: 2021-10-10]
Imatges/Base2.jpg

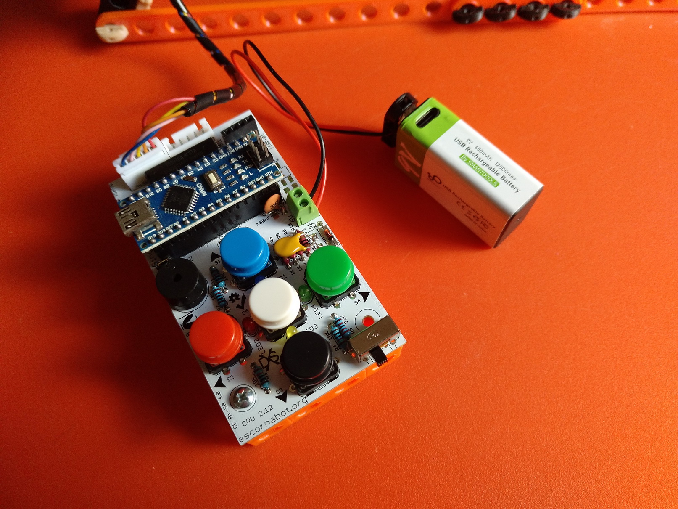
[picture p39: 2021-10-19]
Imatges/MVIMG_20211018_171312_576.jpg

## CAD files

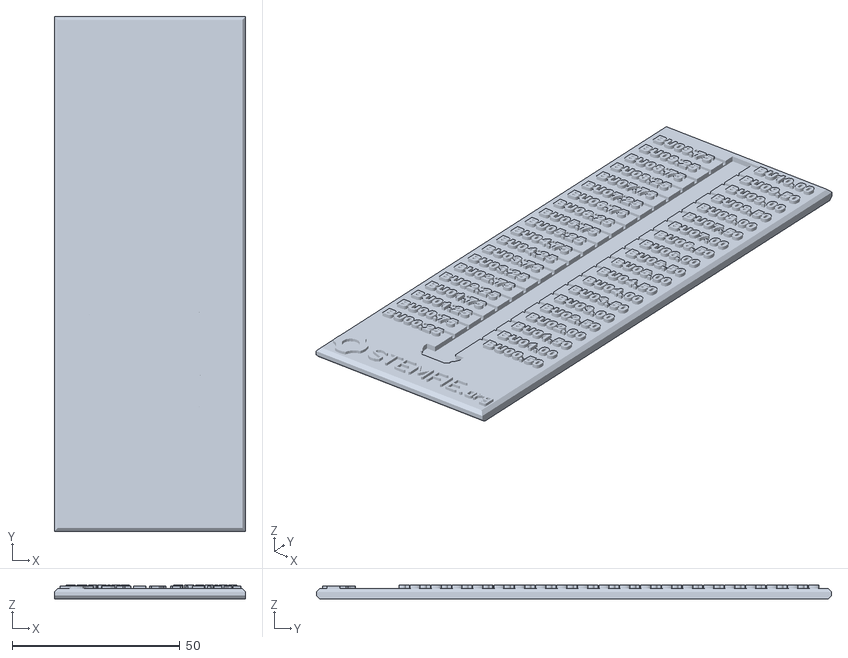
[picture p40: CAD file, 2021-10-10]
STL/Base/MesuraStemfie2.stl
57.0 x 153.4 x 4.13

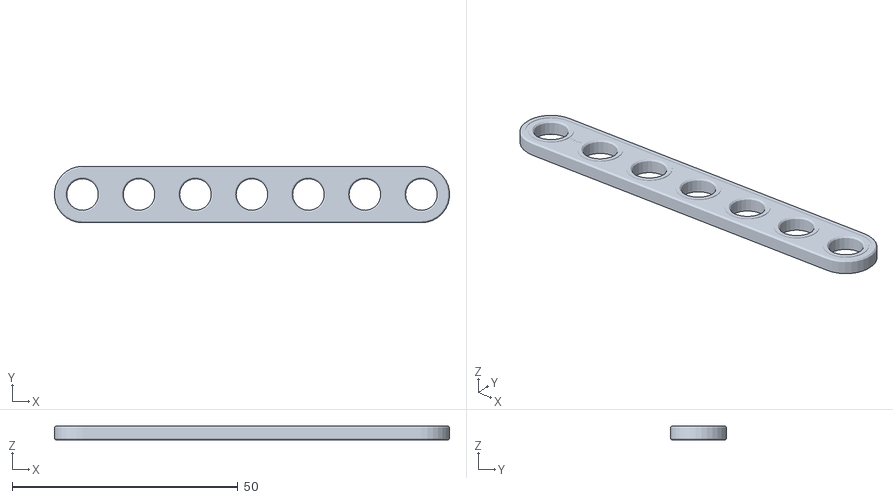
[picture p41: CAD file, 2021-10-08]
STL/Cabin/Brace_7-SPN-BRC-0006_x12.stl
87.4 x 12.5 x 3.12

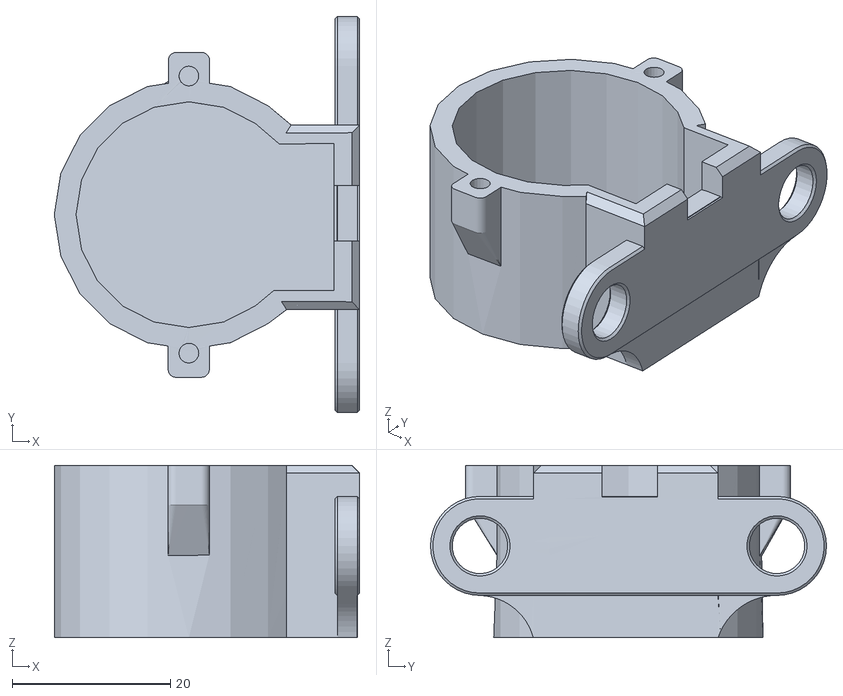
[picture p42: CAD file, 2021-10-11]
STL/Control/28BYJ-48_4H_x1.stl
38.6 x 50.0 x 21.8

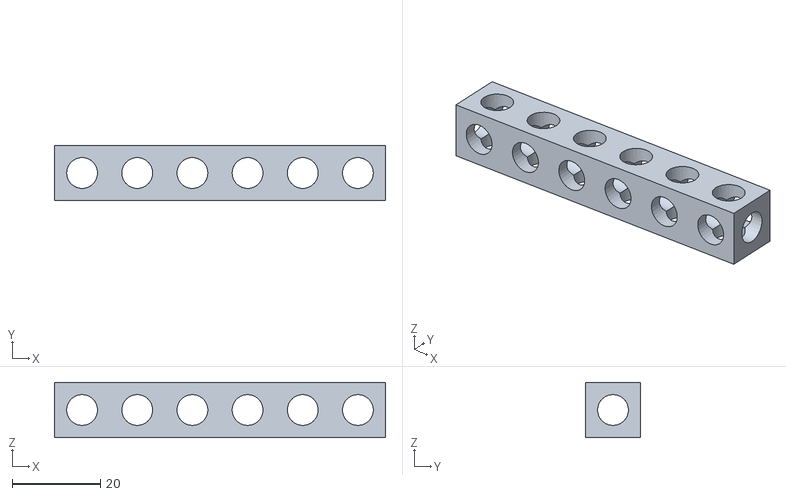
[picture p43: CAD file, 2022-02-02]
STL/Wheel/Beam 1x1x6x3.stl
75.0 x 12.5 x 12.5

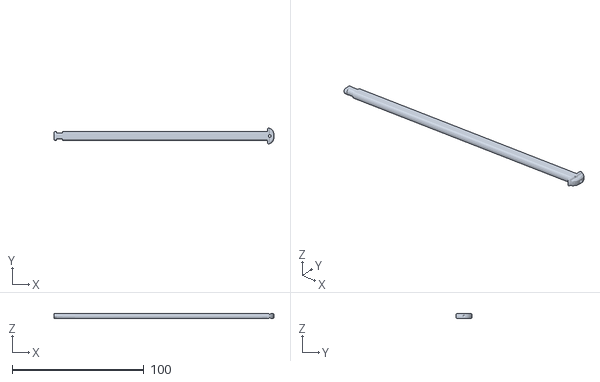
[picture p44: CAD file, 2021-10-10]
STL/Base/Pin166.stl
167.0 x 12.3 x 4.00

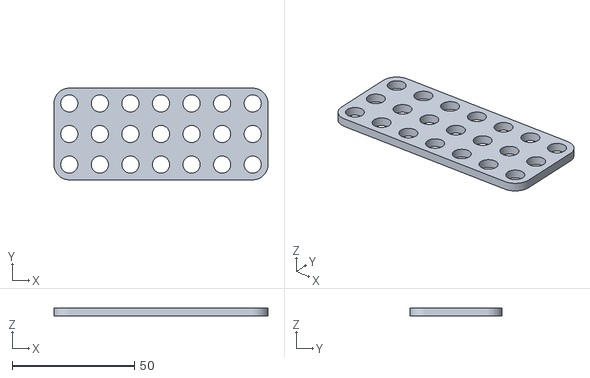
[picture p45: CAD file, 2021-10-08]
STL/Cabin/STR_STD_BRM_7x3_x6.stl
87.5 x 37.5 x 3.25

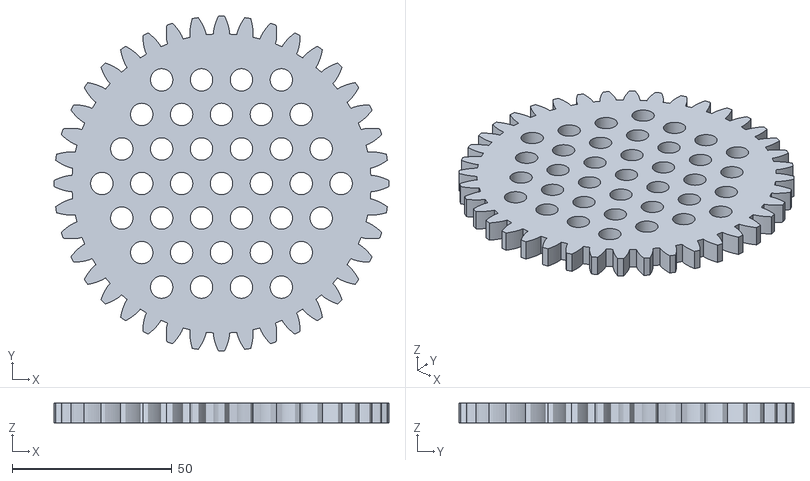
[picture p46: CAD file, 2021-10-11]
STL/Control/IGE_0.5_40_M2,5_x1.stl
105.0 x 105.0 x 6.25

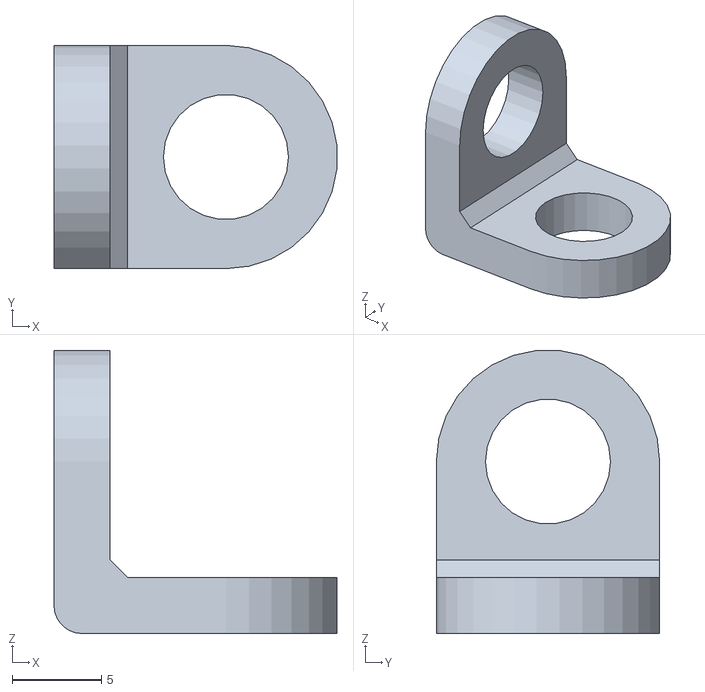
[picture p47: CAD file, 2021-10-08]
STL/Cabin/STR_STD_BRD_AY-1x1_90_x60.stl
15.8 x 12.5 x 15.8

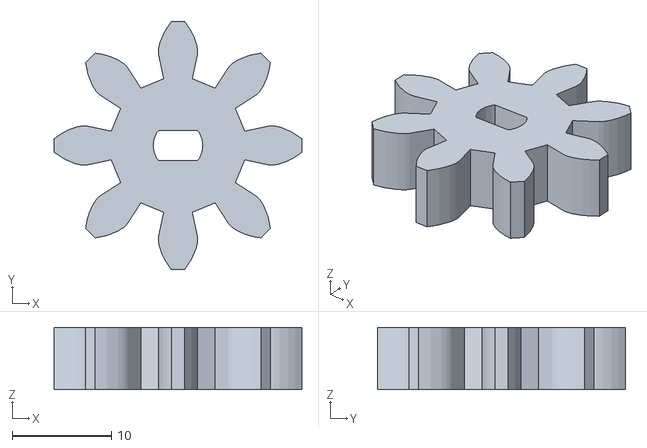
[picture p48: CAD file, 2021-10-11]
STL/Control/Gear_28BYJ-48_x1.stl
25.0 x 25.0 x 6.25

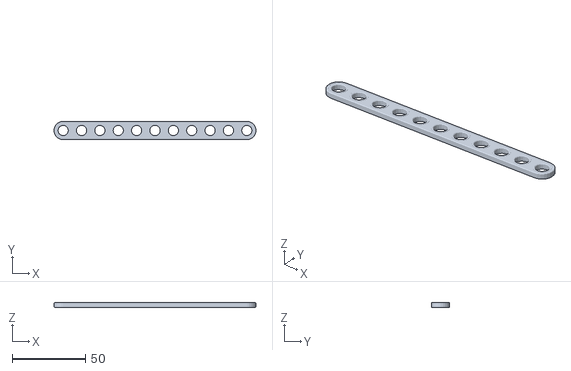
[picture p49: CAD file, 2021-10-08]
STL/Wheel/Brace_11_STR_ERR_x24.stl
137.5 x 12.5 x 3.12

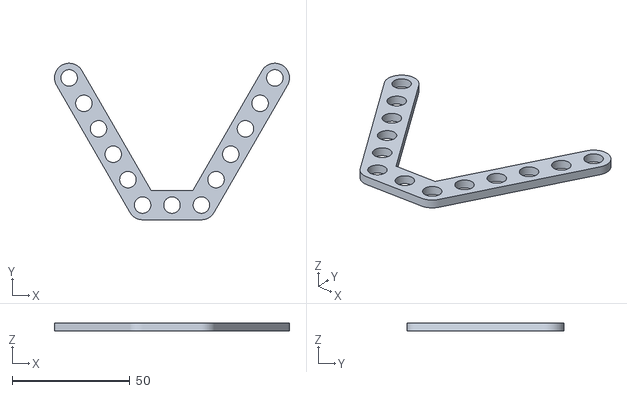
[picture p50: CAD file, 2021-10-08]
STL/Base/STR_STD_BRT_AZ_3_5_5_120_x4.stl
100.0 x 66.6 x 3.25

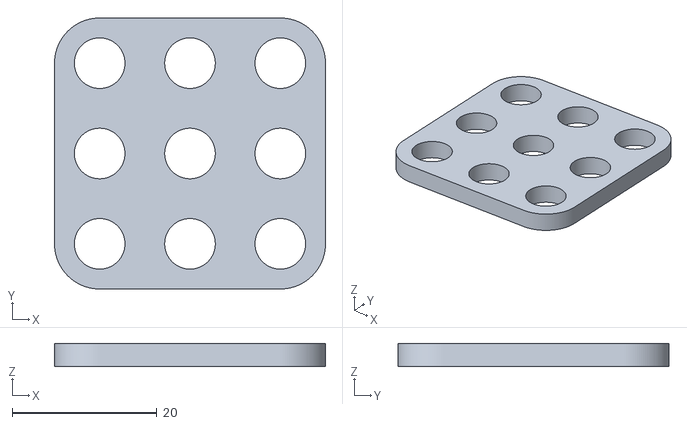
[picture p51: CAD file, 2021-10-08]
STL/Cabin/STR_STD_BRM_3x3_x12.stl
37.5 x 37.5 x 3.25

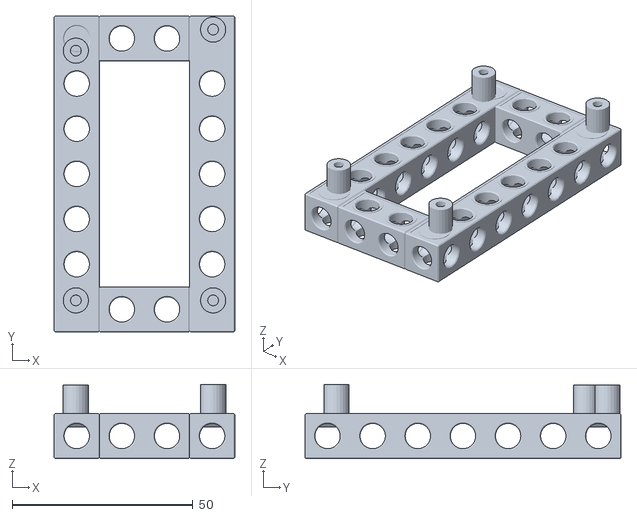
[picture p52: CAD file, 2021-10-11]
STL/Control/CPUEscornaStemfie_x1.stl
50.0 x 87.5 x 20.6

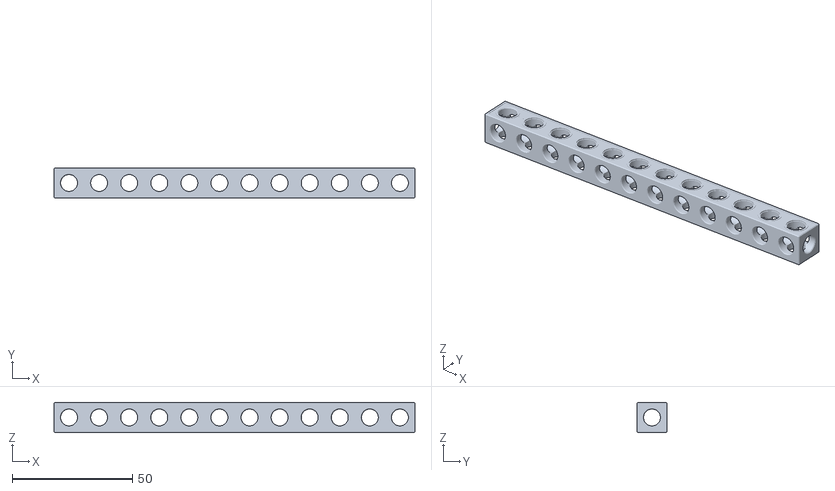
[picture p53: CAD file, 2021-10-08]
STL/Base/Beam_12_x8.stl
150.0 x 12.5 x 12.5

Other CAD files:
STL/Cabin/STR_STD_BRT-AYx1x3x1_x12.stl
STL/Cabin/STR_STD_BRT_AZ_5x5x5_x12.stl
STL/Wheel/Pin_CL_RHD_BU07.00_x6.stl
STL/Base/Brace_4_STR_ERR_BU04x01x00.25_x10.stl
STL/Base/Brace_12_STR_ERR_BU12x01x00.25x4.stl
STL/Base/Brace_13_STR_ERR_BU13x01x00.25_x4.stl
STL/Base/Nut_PH_CL_BU1x5mm_x1.stl
STL/Base/Screw_RHD_RH_BU00.50_x8.stl
STL/Base/Screw_RHD_RH_BU01.25_x12.stl
STL/Cabin/STR_STD_BRM_5x3_x6.stl
STL/Control/Nut_RH_BU01.00x5mm_x5.stl
STL/Control/Screw_RHD_RH_BU01.50_x5.stl
STL/Control/Washer_FRE_BU01.00x00.25_x2.stl
STL/Wheel/Cross_9x9x9_x2.stl
STL/Wheel/Screw_RHD_RH_BU00.75_x12.stl
STL/Wheel/Screw_RHD_RH_BU06.50_x3.stl
STL/Wheel/Washer10mm_12.stl
STL/Wheel/Washer_FRE_2.5mmx2.stl
